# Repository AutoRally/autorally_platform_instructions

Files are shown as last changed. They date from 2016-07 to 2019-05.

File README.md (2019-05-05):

[note]: https://github.com/AutoRally/autorally/wiki/note_icon.png "note"

# AutoRally Platform Instructions

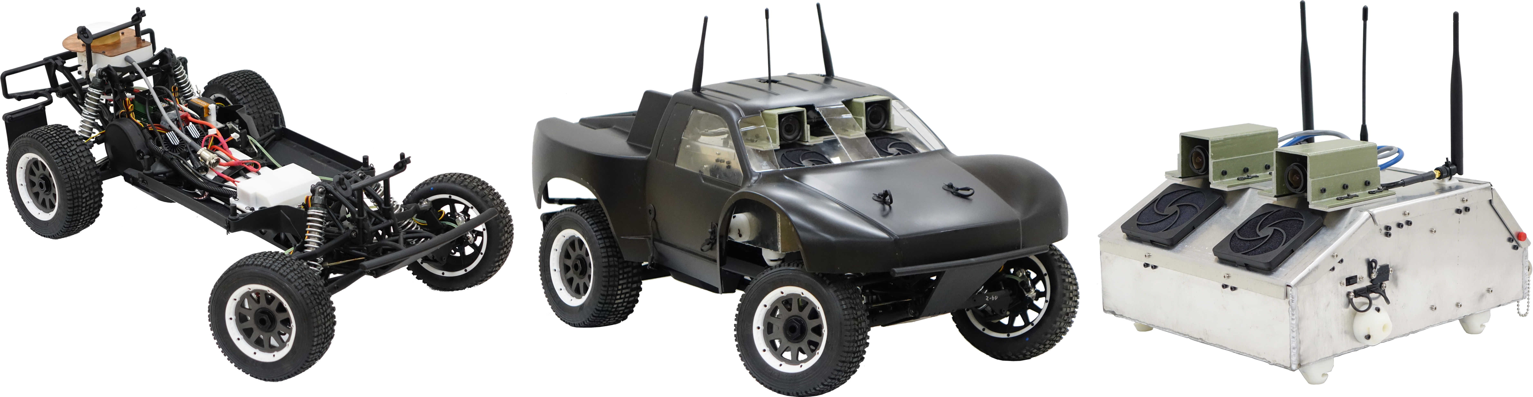
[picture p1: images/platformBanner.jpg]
Platform image


The documents contained in this repository provide all of the information required to construct and operate a complete AutoRally platform. The platform has two primary parts, the chassis and compute box.

A paper detailing the platform and design decisions can be found [here](https://ieeexplore.ieee.org/abstract/document/8616931).

BibTex:
```
@article{goldfain2019autorally,
  title={AutoRally: An Open Platform for Aggressive Autonomous Driving},
  author={Goldfain, Brian and Drews, Paul and You, Changxi and Barulic, Matthew and Velev, Orlin and Tsiotras, Panagiotis and Rehg, James M},
  journal={IEEE Control Systems Magazine},
  volume={39},
  number={1},
  pages={26--55},
  year={2019},
  publisher={IEEE}
}
```

 Please contact us by opening an issue or emailing if you have any questions about the instructions, parts, or any part of the build process.

## Getting Started

Look though the documentation and [Download](https://github.com/AutoRally/autorally_platform_instructions/releases) our latest release. Look over the Getting Started section in the chassis and compute box instruction documents, followed by the parts list and the operating procedures to get a sense of the build process, skill requirements, fabrication methods, and testing procedures. The AutoRally platform can be fabricated by a small team (2-3 students) of non-professionals. The build will go most smoothly if there is at least one person on the team familiar with basic soldering, 3D printing, Ubuntu and ROS configuration. We also link to tutorials for all of the skills required, so any interested party can easily acquire them.

  The most difficult component to fabricate is the compute box enclosure, which may require sending away to a local sheet metal fabrication shop if sheet metal fabrication experience and tools are not available.

Before testing a platform you build, make sure to complete the [Setup Instructions](https://github.com/AutoRally/autorally) and the [Platform Configuration Instructions](https://github.com/AutoRally/autorally/wiki/Platform%20Configuration%20Instructions).

## Included Files:

### autoRally_chassis_instructions

Complete instructions to build an AutoRally chassis.

### autoRally_compute_box_instructions

Complete instructions to build a Mini-ITX AutoRally compute box.

### autoRally_operating_procedures

Document outlining pre-run preparations, starting up and operating the platform, and post-run procedures.

### autoRally_platform_parts_list

Spreadsheet of all parts required to build an AutoRally Platform. The document includes the estimated price, quantities, and link to purchase each component. Parts are organized by vendor, and color coded by where on the platform they are used. The list includes the required parts, parts that help with usability (spare set of batteries), and some common maintenance items.

  The platform uses parts from about 25 suppliers.

  Review the entire list before making any purchases as you may already have some of the parts around such as computer monitors, spare laptops for use as ground station, assorted cables, keyboard and mouse, tools, and supplies. 

### diagrams/

Wiring diagrams for the custom AutoRally chassis and compute box assemblies.

### manuals/

Product manuals for individual parts involved in the build.

### models/

CAD models for components to be fabricated (most will be 3D printed).

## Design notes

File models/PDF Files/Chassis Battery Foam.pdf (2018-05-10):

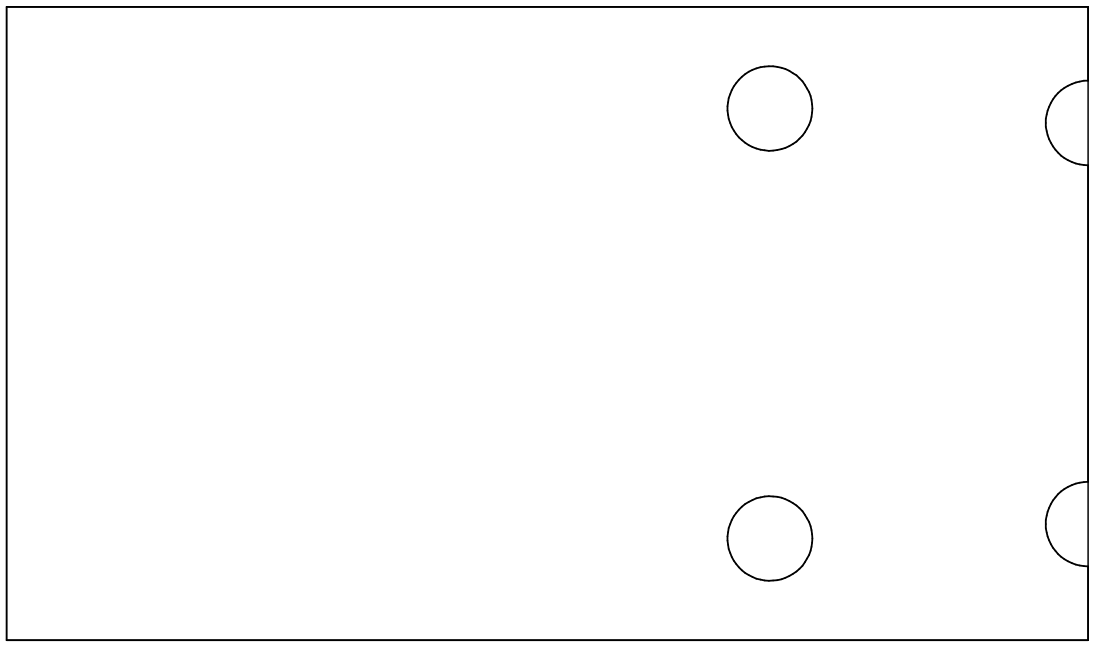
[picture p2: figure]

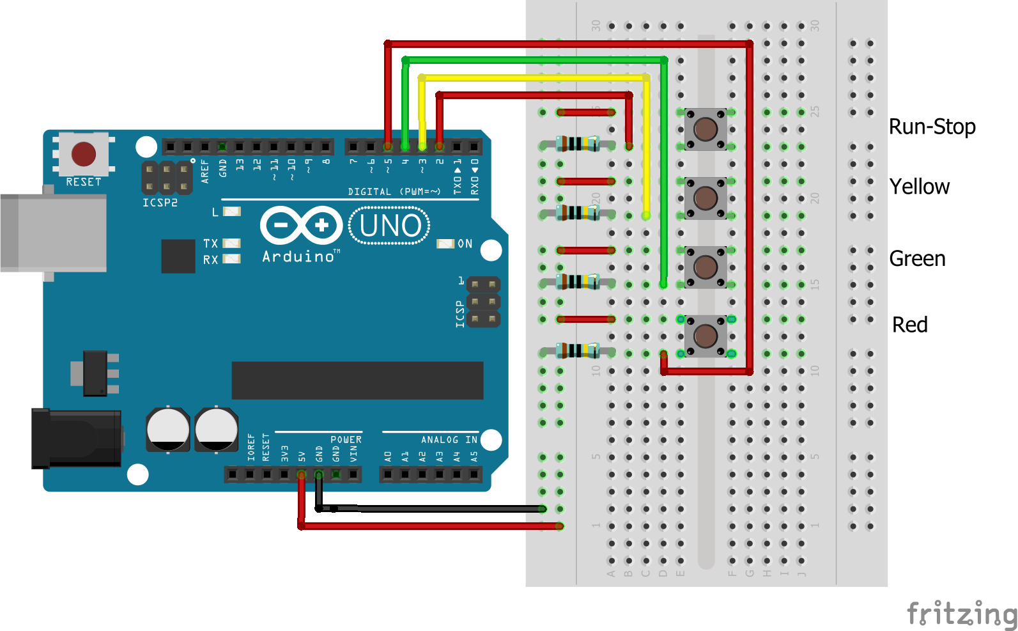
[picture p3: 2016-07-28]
diagrams/AutoRally_RunStop_Schematic_Uno.png

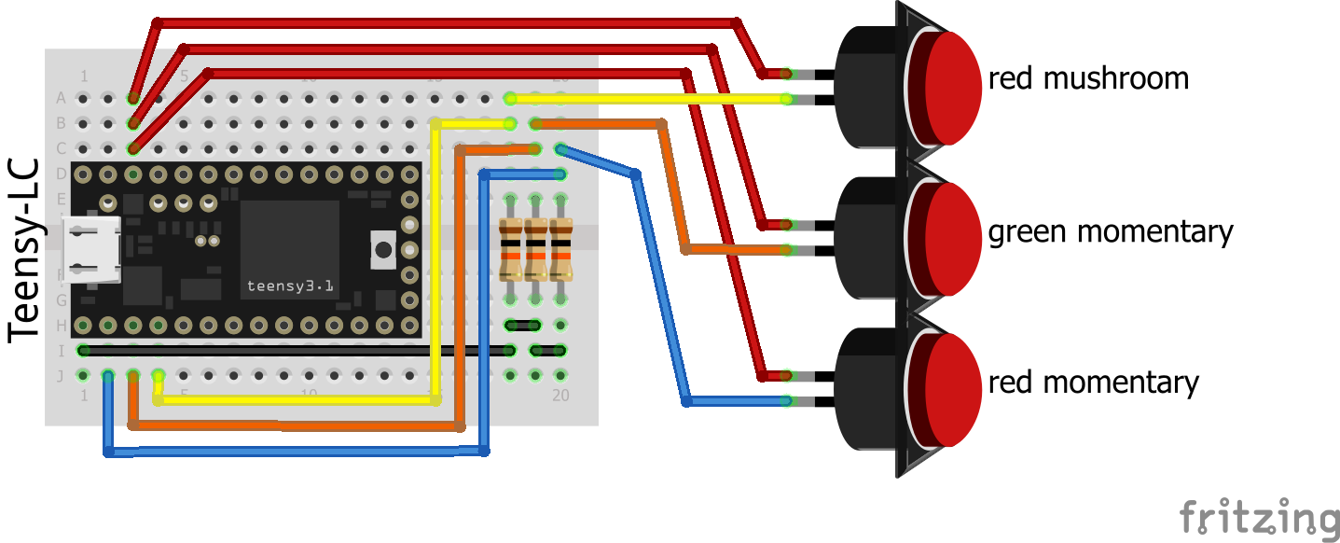
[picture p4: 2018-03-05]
diagrams/AutoRally_RunStop_Schematic_Teensy.png

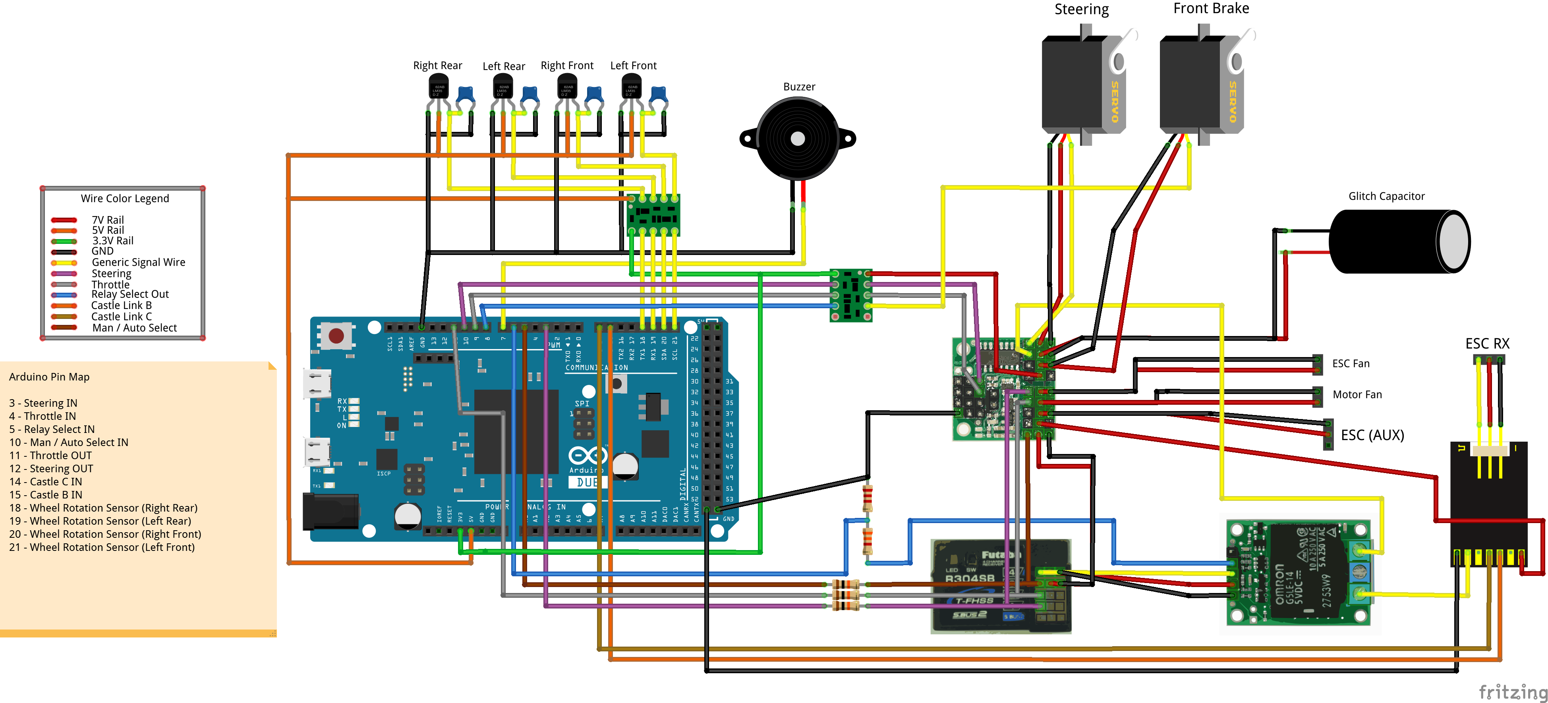
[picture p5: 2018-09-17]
diagrams/AutoRally_Electronics_Box.png

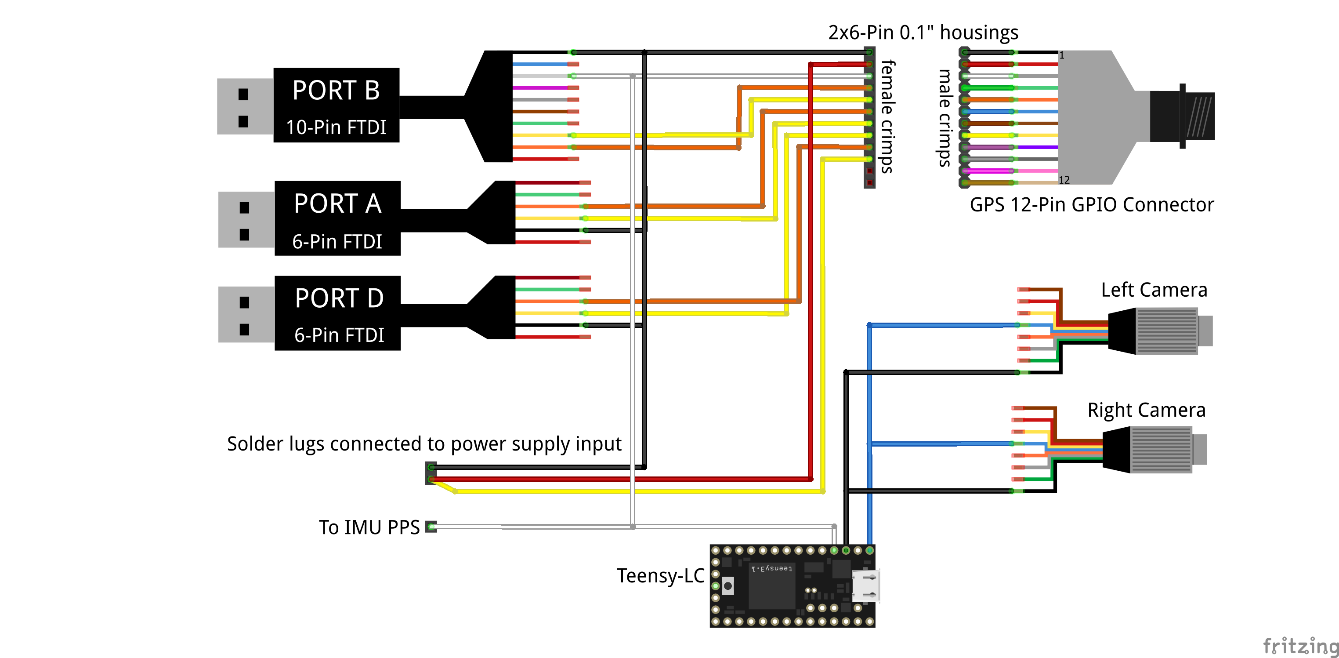
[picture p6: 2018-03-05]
diagrams/AutoRally_ComputeBox_Teensy.png

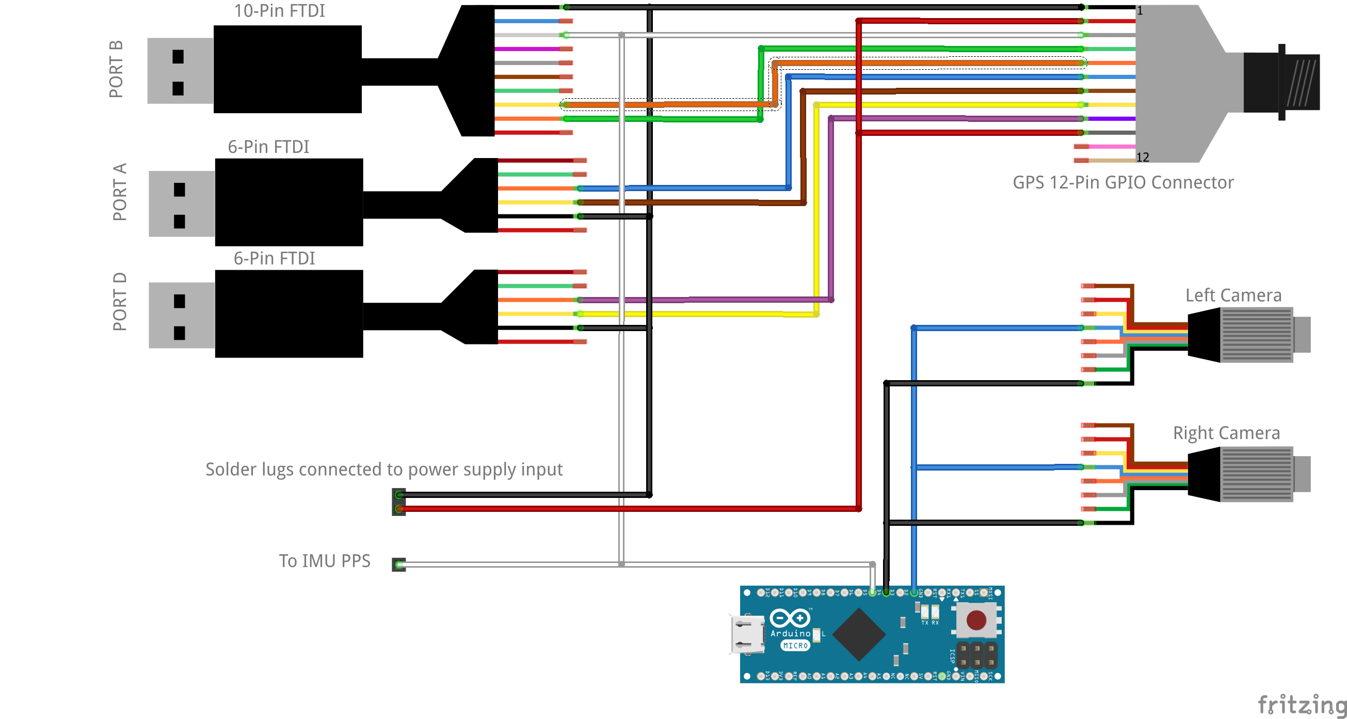
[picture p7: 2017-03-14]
diagrams/AutoRally_ComputeBox_Micro.png

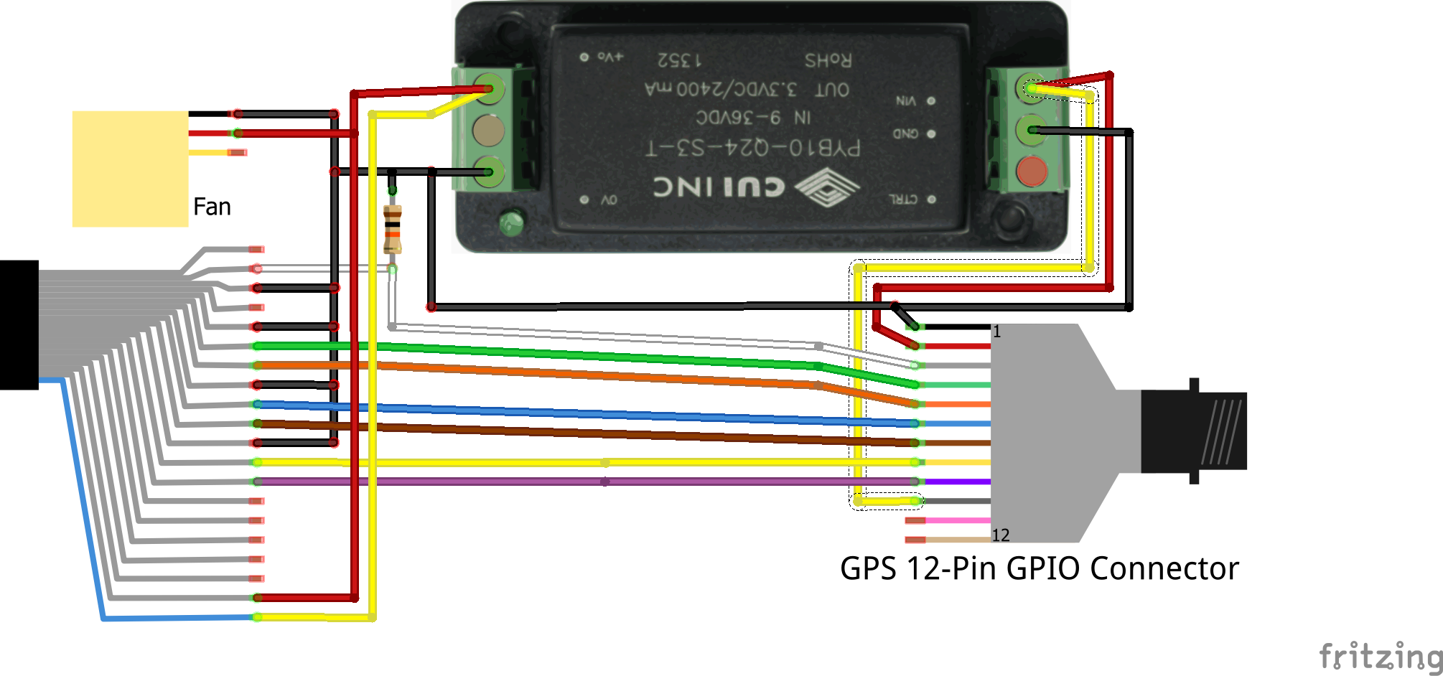
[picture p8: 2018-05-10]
diagrams/AutoRally_GPS_Box.png

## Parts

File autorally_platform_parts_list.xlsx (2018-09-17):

AutoRally Platform Parts List |  |  | Version 1.4 |  | 2018-03-01 |  | Brian Goldfain
This parts list includes all required parts to construct a complete AutoRally chassis and Mini-ITX AutoRally compute box.
Required parts like a monitor, keyboard, and mouse for the compute box, laptop to run operator control station that you likely already have are included in the list, but don't need to be purchased if you already have them.
Tools needed in addition to those included with the chassis are listed at the bottom. There is no need to purchase the tools if you already have access to similar ones.
If your budget allows, the most useful upgrade is a second set of chassis and compute box batteries from MaxAmps.
If you are sending out for the compute box fabrication, you do not need to purchase the raw compute box materials from McMaster
Parts are mostly grouped by seller and each seller is put in a loose category for the platform
 | Color Guide:
 | Compute box raw materials
 | Suggested Maintenance Parts
 | Part Configuration Required Upon Purchase
 | Suggested RTK GPS Base Station Equipment
 | Item | Description | Price | Quantity | Item Totals | Section Totals | Link | Alternate Part
Chassis | RC car chassis | HPI Baja 5SC RTR | $1280.00 | 1 | $1280.00 |  | http://www.davesmotors.com/hpi-109964b-hpi-baja-5sc-1_5-gas-rc-short-course-truck-w_2_4-ghz-radio-black.html
 | Transmitter/Receiver | Futaba 4PV | $279.99 | 1 | $279.99 |  | http://www.davesmotors.com/Futaba-FUTK4700-4PV-4-Channel-T-FHSS-Computer-Radio-System.html
 | Transmitter Battery | LiFe 6.6V 1900mAh 2 Cell Battery | $34.99 | 1 | $34.99 |  | http://www.davesmotors.com/LiFe-6-6V-1900mAh-2-Cell-Battery-Pack.html
 | Battery box eliminator | Team FastEddy Battery Box Eliminator for HPI Baja 5B/5T/5SC | $49.99 | 1 | $49.99 |  | http://www.davesmotors.com/tr800
 | Steering Linkage | Turtle Racing Billet Servo Saver for HPI Baja 5b/5T/5SC | $89.99 | 1 | $89.99 |  | http://www.davesmotors.com/Turtle-Racing-Billet-Servo-Saver-for-HPI-Baja-5b-5T-5SC-TR1481.html
 | Axle extender set | Darksoul V2 Axle Extender Set for HPI Baja 5B/5T/5SC | $59.99 | 1 | $59.99 |  | http://www.davesmotors.com/s.nl/it.A/id.3515/.f
 | Front brakes | Mecatech Front Hydraulic Brake System for HPI Baja 5B/5T/5SC | $329.00 | 1 | $329.00 |  | http://www.davesmotors.com/Mecatech-Front-Hydraulic-Brake-System-for-HPI-Baja-5B-5T-RCTB01013.html
 | Front Tire Foams | Hostile "Zero Growth" Foam Inserts for HPI Baja 5T/5SC Front, and Losi 5ive/DBXL/VEKTA.5 Front/Rear | $44.99 | 1 | $44.99 |  | http://www.davesmotors.com/hostile-zero-growth-foams-hpi-baja-5t-5sc-losi-5ive-desert-buggy-xl-dbxl-HPI4817-LOSB7241-LOS45006.html
 | Rear Tire Foams | Hostile "Zero Growth" Foam Inserts for HPI Baja 5T/5SC Rear | $44.99 | 1 | $44.99 |  | http://www.davesmotors.com/hostile-zero-growth-foams-hpi-baja-5t-5sc-rear-HPI4818-4818.html
 | Alloy Servo Horn 15T | Alloy Horn for Hitec D845/5765/Savox 15T-Spline Servos | $9.99 | 1 | $9.99 |  | http://www.davesmotors.com/alloy-horn-for-multiplex-rhino-digi-4-hitec-5755mg-servo-new-style.html
 | Shock Piston Set | HPI 85413 | $19.99 | 1 | $19.99 |  | http://www.davesmotors.com/hpi-85413-shock-piston-set-for-vvc_hd-shocks.html
 | M4x20mm cap head screws | 10-pack | $1.95 | 1 | $1.95 |  | http://www.davesmotors.com/fg-06725-20-socket-head-cap-screw-set-m4x20mm.html
 | M4x6mm cap head screws | 10-pack | $1.95 | 1 | $1.95 |  | http://www.davesmotors.com/hpi-94502-cap-head-screw-set-m4x6mm.html
 | Body clips 8mm | DDM steel body clips | $3.99 | 1 | $3.99 |  | http://www.davesmotors.com/ddm-steel-body-clips-8mm-for-15-and-18-scale-set-of-50.html
 | Body clips 6mm | HPI 75106 | $5.99 | 1 | $5.99 |  | http://www.davesmotors.com/hpi-75106-body-clip-set-6mm.html
 | Driveshaft | HPI 104966 | $49.49 | 1 | $49.49 |  | http://www.davesmotors.com/hpi-104966-super-heavy-duty-drive-shaft-18x116mm-2pcs.html
 | Front Shock Mounting Set | HPI 85469 | $7.50 | 1 | $7.50 |  | http://www.davesmotors.com/hpi-85469-front-shock-mounting-set.html
 | Axle boots 5SC | HPI 104968, 25x47mm | $11.99 | 2 | $23.98 |  | http://www.davesmotors.com/hpi-104968-axle-boot-25x47mm-4pcs.html
 | Shock Boots Rear | HPI 86443, 20x80mm | $9.99 | 2 | $19.98 |  | http://www.davesmotors.com/hpi-86443-rear-shock-boot-set-20x80mm.html
 | Shock Boots Front | HPI 86442, 20x70mm | $6.30 | 2 | $12.60 |  | http://www.davesmotors.com/hpi-86442-front-shock-boot-set-20x70mm.html
 | Differential Case Gaskets | HPI86478 | $16.99 | 1 | $16.99 |  | http://www.davesmotors.com/hpi-86478-differential-case-gasket-set.html
 | Replacement bearing kit | TeamFastEddy Complete Bearing Upgrade Kit for HPI Baja 5B/5T/5SC | $41.00 | 1 | $41.00 |  | http://www.davesmotors.com/s.nl/it.A/id.4336/.f
 | Axle/transmission grease | Team FastEddy Axle/Transmission Grease | $17.00 | 1 | $17.00 |  | http://www.davesmotors.com/Team-FastEddy-Axle-Transmission-Grease-.html
 | Sway Bar Set | HPI 86618 | $62.99 | 1 | $62.99 |  | http://www.davesmotors.com/hpi-86618-sway-bar-set.html
 | Steering Servo | Savox SV-0235MG | $85.99 | 1 | $85.99 |  | http://www.savoxusa.com/Savox_SV0235MG_Digital_Servo_p/savsv0235mg.htm
 | Brake Servo | Savox SV-1271TG | $79.99 | 1 | $79.99 |  | http://www.savoxusa.com/Savox_SV1271TG_Digital_Servo_p/savsv1271sg.htm
 | Glitch Capacitor | Racer's Edge Glitch Buster Power Capacitor | $5.99 | 1 | $5.99 |  | http://www.savoxusa.com/Glitch_Buster_Power_Capacitor_p/rce2474.htm
 | Electric Conversion Hardware | HPI Baja 5SC Gas to Brushless motor conversion mount kit | $99.99 | 1 | $99.99 |  | https://www.aliexpress.com/item/Rovan-HPI-KM-baja-5B-5T-5SC-Gas-to-Brushless-motor-conversion-mount-kit-851925/32797778803.html
 | Battery Strap Velcro | 20mm x 500mm, 5-pack | $7.99 | 1 | $7.99 |  | https://www.amazon.com/500mm-Rubberized-Non-Slip-Battery-Straps/dp/B01DNFIPAK
 | Heavy duty mounting tape | 1"x50" roll | $4.34 | 1 | $4.34 |  | https://www.amazon.com/Scotch-Indoor-Mounting-1-Inch-125-Inches/dp/B00004Z4A8/
 | Transmitter battery charger | Futaba FUTM1725 | $34.99 | 1 | $34.99 |  | https://www.towerhobbies.com/cgi-bin/wti0001p?&I=LXGFTG
 | Silicone shock fluid | Team Associated Silicone Shock Fluid 60wt, 800cSt | $4.49 | 4 | $17.96 |  | https://www.towerhobbies.com/cgi-bin/wti0001p?&I=LXMZ17
 | Brake Linkage Rod | Linkage rod for MecaTech brakes | $5.23 | 1 | $5.23 |  | https://rc-car-online.de/en/products/y0132-y0132-linkage-rod-for-mecatech-brakes-2-pcs-.html
 | Brake Bleed Kit | FG Filling and ventilation set | $4.48 | 1 | $4.48 |  | https://rc-car-online.de/en/products/fg_9452_02-9452-02-fg-filling-and-ventilation-set.html
 | Throttle Pivot Set | FG Throttle pivot post, 6534/02 | $5.87 | 1 | $5.87 |  | https://rc-car-online.de/en/products/fg_6534_02-6534-02-fg-throttle-pivot-post.html
 | Brake Line | Mecatech brake line, 1 m | $5.98 | 1 | $5.98 |  | https://rc-car-online.de/en/products/mec_1000_62-1000-62-mecatech-brake-line-1-m.html
 | Hydraullic Oil for front brakes | Mecatech brake fluid, 50 ml | $10.85 | 1 | $10.85 |  | https://rc-car-online.de/en/products/mec_1000_60-1000-60-mecatech-brake-fluid-50-ml.html
 | Front Spring |  | $5.53 | 2 | $11.06 |  | http://www.centuryspring.com/compression-spring-10974.html
 | Rear Spring Long |  | $7.83 | 2 | $15.66 |  | http://www.centuryspring.com/compression-spring-2768.html
 | Electric Conversion | Castle Creations 2028 motor and XL-X ESC | $403.71 | 1 | $403.71 |  | http://www.castlecreations.com/en/mamba-xl-x-2028-combo-010-0142-00
 | Castle Serial Link |  | $90.00 | 1 | $90.00 |  | http://www.castlecreations.com/en/serial-link-010-0121-00
 | Castle Link Programmer |  | $20.15 | 1 | $20.15 |  | http://www.castlecreations.com/en/pc-software-and-cables-2/castle-link-v3-usb-programming-kit-011-0119-00
 | Pinion Gear | Castle Creations 14-tooth | $12.07 | 2 | $24.14 |  | http://www.castlecreations.com/en/cc-pinion-mod-1-5-14-tooth-010-0065-24
 | ESC | Castle Creations Mamba XL-X | $193.76 | 1 | $193.76 |  | http://www.castlecreations.com/en/mamba-xl-x-esc-010-0140-00
 | M1.4x6mm screws | 10-pack | $7.80 | 1 | $7.80 |  | http://www.mcmaster.com/#92290a474/=120dvtd
 | M1.4 nuts |  | $2.40 | 4 | $9.60 |  | http://www.mcmaster.com/#91828a005/=120dvjk
 | M3 nylon washer | 100-pack | $2.84 | 1 | $2.84 |  | http://www.mcmaster.com/#95610a530/=120dwf7
 | M3 nylon spacer, 18mm long, 4.5mm OD |  | $1.72 | 6 | $10.32 |  | https://www.mcmaster.com/#93657a508/=1bp3ipn
 | M3x4mm aluminum spacer, 4.5mm OD |  | $0.30 | 10 | $3.00 |  | https://www.mcmaster.com/#94669a097/=1bihasc
 | M3x8mm aluminum spacer, 6mm OD |  | $1.33 | 10 | $13.30 |  | https://www.mcmaster.com/#94669a011
 | M3 hex nut | 100-pack | $2.06 | 2 | $4.12 |  | http://www.mcmaster.com/#90591a250/=120dy5e
 | M3 washer | 100-pack | $1.62 | 1 | $1.62 |  | http://www.mcmaster.com/#93475a210/=131co1z
 | Knob with screw head mount, M3, red | 50-pack | $8.48 | 1 | $8.48 |  | https://www.mcmaster.com/#91175a061/=1bmmsv0
 | M3x6mm screw | 100-pack | $8.56 | 1 | $8.56 |  | http://www.mcmaster.com/#91292a111/=12yr76o
 | M3x8mm screw | 100-pack | $6.58 | 1 | $6.58 |  | http://www.mcmaster.com/#91290a113/=120e123
 | M3x10mm screw | 100-pack | $4.40 | 1 | $4.40 |  | http://www.mcmaster.com/#91292a113/=131cnd2
 | M3x12mm screw | 100-pack | $7.75 | 1 | $7.75 |  | http://www.mcmaster.com/#91290a117/=120e45y
 | M3x16mm screw | 100-pack | $8.20 | 1 | $8.20 |  | http://www.mcmaster.com/#91290a120/=120epou
 | M3x20mm screw | 100-pack | $6.18 | 1 | $6.18 |  | https://www.mcmaster.com/#91292a123/=1bjm0lf
 | M3x25mm screw | 25-pack | $4.80 | 1 | $4.80 |  | https://www.mcmaster.com/#91274a111/=1biy8za
 | M3x35mm screw | 25-pack | $3.40 | 1 | $3.40 |  | https://www.mcmaster.com/#91292a033/=1bhdb06
 | M3x40mm screw | 25-pack | $2.39 | 1 | $2.39 |  | https://www.mcmaster.com/#orders/=1biy9ci
 | M3x50mm screw, for front brakes | 25-pack | $3.39 | 1 | $3.39 |  | http://www.mcmaster.com/#91290a137/=120e644
 | 6-32x1/4" screw | 25-pack | $2.67 | 1 | $2.67 |  | http://www.mcmaster.com/#92185a144/=120dvzz
 | Split loom, 1/2" OD, 5ft |  | $2.52 | 1 | $2.52 |  | http://www.mcmaster.com/#7840k72/=120duy7
 | Rear Spring Short | 6-pack | $11.09 | 1 | $11.09 |  | http://www.mcmaster.com/#9657k408/=zybqrr
 | M4 aluminum spacer, 6mm long, 8mm OD |  | $1.38 | 8 | $11.04 |  | http://www.mcmaster.com/#94669a041/=120elfz
 | M4 nuts | 100-pack | $2.28 | 1 | $2.28 |  | http://www.mcmaster.com/#90591a255/=120em4k
 | M4 washer | 100-pack | $1.86 | 1 | $1.86 |  | https://www.mcmaster.com/#93475a230/=16qk6oh
 | M4x14mm screw | 100-pack | $9.55 | 1 | $9.55 |  | http://www.mcmaster.com/#91290a150/=120enm4
 | M5x16mm button head screws | 10-pack | $8.33 | 1 | $8.33 |  | https://www.mcmaster.com/#97763a822/=1bc84k6
 | 4-40x1/2inch screw | 100-pack | $4.05 | 1 | $4.05 |  | http://www.mcmaster.com/#91773a110/=1382r89
 | 16awg power cable, yellow | 10-ft | $11.40 | 1 | $11.40 |  | https://www.mcmaster.com/#8041k52/=16kwi63
 | Spade Terminal | 100-pack | $8.15 | 1 | $8.15 |  | http://www.mcmaster.com/#69145k59/=12uorg8
 | Clevis Pin 3/8" dia, 5/16" usable | 10-pack | $7.52 | 1 | $7.52 |  | http://www.mcmaster.com/#92390a100/=128m34x
 | Stainless Steel Hinge | 1 ft, 1" Width, 0.133" Knuckle Diameter | $3.33 | 1 | $3.33 |  | https://www.mcmaster.com/#1582a457/=14kexr6
 | Structural Fiberglass 2" rect tube | 5 ft | $30.79 | 1 | $30.79 |  | http://www.mcmaster.com/#8548k23/=128m659
 | Structural fiberglass angle 1"x1" | 5 ft | $9.65 | 1 | $9.65 |  | http://www.mcmaster.com/#8542k51/=128m6ms
 | 6"x12" 6061 Aluminum 0.125" thick |  | $6.86 | 1 | $6.86 |  | https://www.mcmaster.com/#8975k921/=163ji4z
 | 6"x12" 6061 aluminum, 0.25" thick |  | $13.37 | 1 | $13.37 |  | http://www.mcmaster.com/#8975k437/=128mro8
 | 24x36" 3003 aluminum sheet, 0.09" thick |  | $45.97 | 1 | $45.97 |  | http://www.mcmaster.com/#8973k68/=128m88a
 | 12"x24" 5/64" thick clear acrylic sheet |  | $8.15 | 1 | $8.15 |  | https://www.mcmaster.com/#8589k22/=1b53vt2
 | Zip ties, 4" | 100-pack | $2.43 | 2 | $4.86 |  | http://www.mcmaster.com/#7130k52/=120erv8
 | Zip ties, 8.5" | 50-pack | $3.50 | 1 | $3.50 |  | http://www.mcmaster.com/#7130k104/=120evi5
 | Zip tie saddle | 25-pack | $3.43 | 2 | $6.86 |  | http://www.mcmaster.com/#7566k73/=120ew2s
 | Liquid electrical tape, 4oz black |  | $7.89 | 1 | $7.89 |  | http://www.mcmaster.com/#76425a51/=120exoz
 | Liquid electrical tape, 4oz red |  | $7.89 | 1 | $7.89 |  | http://www.mcmaster.com/#76425a51/=120eyab
 | Loctite 243 | 0.34 oz | $13.63 | 1 | $13.63 |  | http://www.mcmaster.com/#91458a115/=120e79s
 | Chassis battery pair, matching 4S 9000mah | 6.5 mm gold female | $489.99 | 1 | $489.99 |  | https://www.maxamps.com/maxamps-lipo-9000xl-4s-14-8v-pair-for-8s-x-maxx
 | Compute box battery, 6s 11Ah | 6.5 mm gold female | $399.99 | 1 | $399.99 |  | http://www.maxamps.com/proddetail.php?prod=Lipo-11000-222-Pack
 | Battery Charger and power supply | 6.5mm Gold Male plugs and Dual output 24V power supply | $456.98 | 1 | $456.98 |  | http://www.maxamps.com/EOS0720i-DUO3-6151.htm
 | 6.5mm bullet connectors | Castle Gold connectors | $6.49 | 6 | $38.94 |  | http://www.maxamps.com/Castle-65mm-SET.htm
 | 4mm banana plug |  | $4.00 | 4 | $16.00 |  | http://www.maxamps.com/4mm-SET.htm
 | Noodle Wire 16awg Red | Per foot | $0.99 | 5 | $4.95 |  | http://www.maxamps.com/16AWG-RED.htm
 | Noodle Wire 16awg Black | Per foot | $0.99 | 5 | $4.95 |  | http://www.maxamps.com/16AWG-BLACK.htm
 | Heavy Duty Servo Wire 50' |  | $14.95 | 1 | $14.95 |  | https://www.servocity.com/50-0-heavy-duty-hitec-standard-wire
 |  |  |  |  |  | $5424.14
Sensors and Electronics | Camera | Part FLIR BFS-U3-13Y3C-C , Blackfly S Color 1.3 MP USB3, 1280x1024 | $395.00 | 2 | $790.00 |  | https://www.ptgrey.com/blackfly-s-13-mp-color-usb3-vision-on-semi-python1300
 | Camera GPIO Cable | Part ACC-01-3009, 1m, 6 pins, Hirose HR10 | $25.00 | 2 | $50.00 |  | https://www.ptgrey.com/1-meter-circular-6-pin-pre-wired-gpio-hirose-connector
 | Camera Lens | Part 68-672, c-mount, 3.5mm fixed focal length | $375.00 | 2 | $750.00 |  | https://www.edmundoptics.com/imaging-lenses/fixed-focal-length-lenses/3.5mm-fl-compact-fixed-focal-length-lens/
 | USB A to B, 6 in |  | $2.95 | 1 | $2.95 |  | https://www.adafruit.com/product/900
 | USB A to mini-B, 6in |  | $2.95 | 1 | $2.95 |  | https://www.adafruit.com/product/899
 | HDMI Panel Mount |  | $5.95 | 1 | $5.95 |  | https://www.adafruit.com/products/978
 | Ethernet Panel Mount |  | $4.95 | 1 | $4.95 |  | https://www.adafruit.com/product/909
 | Buzzer, 5V |  | $0.95 | 2 | $1.90 |  | https://www.adafruit.com/product/1536
 | Tiny Breadboard |  | $4.00 | 1 | $4.00 |  | https://www.adafruit.com/product/65
 | IMU, Microstrain 3DM-GX5-25 | 900 deg/s, 20g calibration | $1495.00 | 1 | $1495.00 |  | http://www.microstrain.com/inertial/3dm-gx5-25
 | IMU cable, Mini-DB9 |  | $45.00 | 1 | $45.00 |  | LORD Microstrain part number 6224-0100
 | WiFi Antenna Cable | RP-SMA, 1.75 ft | $17.40 | 2 | $34.80 |  | http://fieldcomponents.com/RPSMAF-LMR240-RPSMAM-Length.html
 | GPS Antenna cable | MCX Male to TNC Male, 0.75 ft | $25.48 | 2 | $50.96 |  | https://fieldcomponents.com/RMCXM-RG316DS-RTNCM-Length.html
 | GPS, Hemisphere Eclipse P307 GPS | 20-pin module with 20Hz, L1/L2, RTK, GLONASS activations included | $270.00 | 1 | $270.00 |  | https://www.subseatechnologies.com/hemisphere-gnss/oem-modules/p306-p307/
 | Hemisphere GNSS OEM Board Universal Development Kit with activations | Must get this UDK to get overall cheaper price for GPS | $1650.00 | 1 | $1650.00 |  | https://www.subseatechnologies.com/hemisphere-gnss/udk/
 | GPS rover antenna, multi-constellation | Antcom 2GNSSA-XT-1 | $578.00 | 1 | $578.00 |  | http://www.navtechgps.com/departments/equipment/antennas/gnss/antcom_active_l1/l2/l5/l_band_gps_and_l1/l2_glonass_in_2_6_diameter_fixed_mount_configuration/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
 | Servo Multiplexor |  | $10.00 | 2 | $20.00 |  | http://www.pololu.com/product/2806
 | RC Switch |  | $10.00 | 2 | $20.00 |  | http://www.pololu.com/product/2804
 | Level Shifter |  | $2.25 | 5 | $11.25 |  | https://www.pololu.com/product/2595
 | 0.1" Straight Male Header |  | $1.00 | 1 | $1.00 |  | http://www.pololu.com/product/965
 | Stranded Wire: Blue, 26 AWG, 70 Feet |  | $4.50 | 1 | $4.50 |  | http://www.pololu.com/product/2626
 | Stranded Wire: Yellow, 26 AWG, 70 Feet |  | $4.50 | 1 | $4.50 |  | http://www.pololu.com/product/2624
 | Stranded Wire: Red, 26 AWG, 70 Feet |  | $4.50 | 1 | $4.50 |  | http://www.pololu.com/product/2622
 | Stranded Wire: Black, 26 AWG, 70 Feet |  | $4.50 | 1 | $4.50 |  | https://www.pololu.com/product/2620
 | 2x5 Pin 0.1" crimp housing | 5-pack | $0.69 | 1 | $0.69 |  | https://www.pololu.com/product/1913
 | 2x6 Pin 0.1" crimp housing | 5-pack | $0.79 | 1 | $0.79 |  | https://www.pololu.com/product/1914
 | 1x1 Pin 0.1" crimp housing | 25-pack | $0.59 | 1 | $0.59 |  | https://www.pololu.com/product/1900
 | 2x1 Pin 0.1" crimp housing | 25-pack | $0.69 | 1 | $0.69 |  | https://www.pololu.com/product/1901
 | 3x1 Pin 0.1" crimp housing | 25-pack | $0.79 | 2 | $1.58 |  | https://www.pololu.com/product/1902
 | 4x1 Pin 0.1" crimp housing | 10-pack | $0.59 | 1 | $0.59 |  | https://www.pololu.com/product/1903
 | 5x1 Pin 0.1" crimp housing | 10-pack | $0.69 | 1 | $0.69 |  | https://www.pololu.com/product/1904
 | 7x1 Pin 0.1" crimp housing | 10-pack | $0.89 | 1 | $0.89 |  | https://www.pololu.com/product/1906
 | Female Crimps |  | $6.00 | 2 | $12.00 |  | http://www.pololu.com/product/1930
 | Male crimps |  | $8.00 | 1 | $8.00 |  | http://www.pololu.com/product/1931
 | Futaba J Connector Female |  | $1.95 | 4 | $7.80 |  | https://www.pololu.com/product/1926
 | Futaba J Connector Male |  | $2.95 | 4 | $11.80 |  | http://www.pololu.com/product/1927
 | Teensey LC |  | $14.65 | 2 | $29.30 |  | https://www.pjrc.com/store/teensylc_pins.html
 | 1/8 inch Magnets | 10-pack | $1.40 | 5 | $7.00 |  | https://www.kjmagnetics.com/proddetail.asp?prod=D21B-N52
 | 2m waterproof usb 2 connector |  | $23.39 | 1 | $23.39 |  | http://www.l-com.com/usb-usb-cable-waterproof-type-a-male-standard-type-b-male-20m
 | 0.5m waterproof panel mount usb 2 |  | $19.53 | 1 | $19.53 |  | http://www.l-com.com/usb-usb-cable-waterproof-panel-mount-type-a-female-standard-type-a-male-05m
 | USB 3.0 A to microB, 0.5m |  | $18.13 | 2 | $36.26 |  | http://www.l-com.com/usb-usb-30-cable-type-micro-b-a-with-thumbscrew-hardware-05m
 | USB Isolator |  | $149.00 | 1 | $149.00 |  | https://www.sealevel.com/product/iso-1-seaiso-single-port-inline-usb-isolator-ul-recognized/
 |  |  |  |  |  | $6117.30
Computing | ASRock Z270M-ITX/ac | LGA 1151 | $108.99 | 1 | $108.99 |  | https://www.newegg.com/Product/Product.aspx?item=N82E16813157742
 | i7 quad 65 W | i7-7700, LGA1151 | $304.99 | 1 | $304.99 |  | https://www.newegg.com/Product/Product.aspx?Item=N82E16819117727
 | GTX 1050Ti SC 4GB |  | $157.99 | 1 | $157.99 |  | https://www.newegg.com/Product/Product.aspx?item=N82E16814487291
 | 32GB DDR4 RAM |  | $309.99 | 1 | $309.99 |  | http://www.newegg.com/Product/Product.aspx?Item=N82E16820231971
 | 1TB M.2 2280 SSD |  | $448.00 | 1 | $448.00 |  | https://www.newegg.com/Product/Product.aspx?Item=N82E16820147595
 | CPU Cooler | Noctua NH-L9i | $39.19 | 1 | $39.19 |  | http://www.newegg.com/Product/Product.aspx?Item=N82E16835608029
 | 4-Pin fan power cable splitter | Noctua NA-SYC1 | $7.95 | 1 | $7.95 |  | https://www.newegg.com/Product/Product.aspx?Item=9SIA9PV3Y61943
 | USB 3.0 19-pin panel mount |  | $14.12 | 1 | $14.12 |  | http://www.newegg.com/Product/Product.aspx?Item=9SIA24G3KG0688
 | USB 3 4-port hub |  | $8.99 | 1 | $8.99 |  | https://www.newegg.com/Product/Product.aspx?item=9SIA6PF5SY4083
 | Gamepad |  | $19.99 | 1 | $19.99 |  | http://www.newegg.com/Product/Product.aspx?Item=N82E16826104402
 | 8 inch P4 extension cable |  | $2.29 | 1 | $2.29 |  | https://www.newegg.com/Product/Product.aspx?Item=9SIA6705VF9079
 | Wifi antenna pair 2.4/5.8 ghz |  | $5.99 | 4 | $23.96 |  | http://www.newegg.com/Product/Product.aspx?Item=9SIA3M31HT9189
 | USB 3.0 hub, 7 port with power supply |  | $24.99 | 1 | $24.99 |  | https://www.newegg.com/Product/Product.aspx?Item=9SIA1DS14S2069
 | Wireless keyboard/mouse |  | $34.19 | 1 | $34.19 |  | https://www.newegg.com/Product/Product.aspx?Item=N82E16823126188
 | Computer Monitor | for compute box, 27 inch QHD w/ HDMI input | $329.00 | 1 | $329.00 |  | https://www.newegg.com/Product/Product.aspx?Item=N82E16824014591&ignorebbr=1
 | Y-PWR Hot Swap |  | $20.00 | 1 | $20.00 |  | http://www.mini-box.com/Y-PWR-Hot-Swap-Load-Sharing-Controller
 | M4-ATX power supply |  | $90.00 | 1 | $90.00 |  | http://www.mini-box.com/M4-ATX
 | GPS box fan |  | $19.93 | 1 | $19.93 |  | http://www.digikey.com/product-detail/en/UF3F3-500/259-1532-ND/1953953
 | 20 pin GPS ribbon Cable |  | $7.48 | 2 | $14.96 |  | http://www.digikey.com/product-detail/en/TCSD-10-S-12.00-01-N/SAM8541-ND/1106679
 | USB micro plug breakout |  | $3.95 | 2 | $7.90 |  | http://www.digikey.com/product-search/en?keywords=1568-1192-ND
 | Capacitors |  | $0.32 | 10 | $3.20 |  | http://www.digikey.com/product-detail/en/SR151A200JAR/478-7724-ND/3661264
 | 820 Ohm Resistor, 1/4W |  | $0.04 | 10 | $0.40 |  | http://www.digikey.com/product-detail/en/CF14JT820R/CF14JT820RCT-ND/1830348
 | 2 Ohm resistor, 3W |  | $0.57 | 10 | $5.70 |  | https://www.digikey.com/product-detail/en/vishay-bc-components/AC03000002008JAC00/PPC3W2.0CT-ND/596625
 | 2.2 kOhm resistor, 1/4W |  | $0.04 | 10 | $0.40 |  | https://www.digikey.com/product-detail/en/stackpole-electronics-inc/CF14JT2K20/CF14JT2K20CT-ND/1830358
 | 3.3 kOhm resistor, 1/4W |  | $0.04 | 10 | $0.40 |  | https://www.digikey.com/product-detail/en/stackpole-electronics-inc/CF14JT3K30/CF14JT3K30CT-ND/1830362
 | 10 kOhm resistor, 1/4W |  | $0.03 | 25 | $0.72 |  | https://www.digikey.com/product-detail/en/stackpole-electronics-inc/CF14JT10K0/CF14JT10K0CT-ND/1830374
 | Hall Effect Sensors |  | $1.67 | 10 | $16.70 |  | http://www.digikey.com/product-search/en?mpart=OH090U&vendor=365
 | Arduino Due |  | $37.40 | 1 | $37.40 |  | http://www.digikey.com/product-search/en?keywords=1050-1049-ND
 | Due protoshield |  | $14.95 | 1 | $14.95 |  | http://www.digikey.com/product-search/en?keywords=1528-1048-ND
 | Copper foil sheet 11.5 inch x 12 inch |  | $16.54 | 2 | $33.08 |  | http://www.digikey.com/product-detail/en/3m-tc/11.5X12-6-1126/3M9885-ND/2649430
 | EMI Sheilding Textile, 1 inch width, 33 m long |  | $73.10 | 1 | $73.10 |  | https://www.digikey.com/products/en?keywords=732-10216-ND
 | CUI 3.3V 2.4A isolated power supply for GPS |  | $33.35 | 1 | $33.35 |  | http://www.digikey.com/products/en?keywords=PYB10-Q24-S3-T
 | 80mm fan cover |  | $1.60 | 2 | $3.19 |  | http://www.digikey.com/product-detail/en/WMG80M/1053-1402-ND/2621308
 | 80mm EMI filter guard |  | $8.31 | 2 | $16.62 |  | http://www.digikey.com/product-search/en?keywords=Q330-ND
 | 80mm fan filter guard assembly |  | $1.76 | 2 | $3.52 |  | http://www.digikey.com/product-search/en?keywords=1053-1394-nd
 | UART-USB 3.3V |  | $26.00 | 1 | $26.00 |  | http://www.digikey.com/product-search/en?mpart=C232HD-DDHSP-0&vendor=768
 | TTL-USB 3.3V |  | $24.64 | 2 | $49.28 |  | http://www.digikey.com/product-search/en?mpart=TTL-232RG-VREG3V3-WE&vendor=768
 | LED IP-67 |  | $12.81 | 1 | $12.81 |  | http://www.digikey.com/product-search/en?keywords=679-2750-ND
 | XBee Pro 900 MHz RPSMA |  | $39.00 | 2 | $78.00 |  | http://www.digikey.com/product-search/en?keywords=602-1299-ND
 | XBee adapter board |  | $24.99 | 2 | $49.98 |  | http://www.digikey.com/product-detail/en/32400/32400-ND/2666947
 | 900 MHz whip antenna |  | $20.00 | 1 | $20.00 |  | http://www.digikey.com/product-search/en?keywords=A09-HSM-7-ND
 | 900 MHz duck antenna |  | $9.00 | 1 | $9.00 |  | http://www.digikey.com/product-detail/en/digi-international/A09-HASM-7/A09-HASM-7-ND/3482047
 | RPSMA cable 12 inch |  | $10.00 | 1 | $10.00 |  | http://www.digikey.com/product-search/en?keywords=602-1066-ND
 | Power button |  | $13.23 | 1 | $13.23 |  | http://www.digikey.com/product-detail/en/ULV4F2BSS544/EG5194-ND/5299304
 | Reset button |  | $11.53 | 1 | $11.53 |  | http://www.digikey.com/product-search/en?keywords=EG5192-ND
 | Rocker Switch |  | $3.26 | 1 | $3.26 |  | https://www.digikey.com/product-detail/en/e-switch/WB242D1121/EG4758-ND/2116237
 | 80 mm x 25 mm fan |  | $16.94 | 2 | $33.88 |  | http://www.digikey.com/product-search/en?keywords=603-1763-ND
 | 4-pin fan connector |  | $0.89 | 5 | $4.45 |  | http://www.digikey.com/product-search/en?keywords=WM3285-ND
 | Fan connector crimps |  | $0.11 | 25 | $2.84 |  | http://www.digikey.com/product-detail/en/0008500114/WM1114-ND/26475
 | USB dust cover |  | $1.58 | 5 | $7.90 |  | http://www.digikey.com/product-search/en?keywords=MUSB-2A111-024BP-ND
 | Ethernet dust cap |  | $0.59 | 5 | $2.95 |  | https://www.digikey.com/product-detail/en/wurth-electronics-inc/726154101/732-3804-ND/3124561
 | 0.1” header keying plug |  | $0.15 | 10 | $1.52 |  | http://www.digikey.com/product-search/en?keywords=askp01-nd
 | 12 position plug | Hirose RM, 15mm | $20.17 | 1 | $20.17 |  | https://www.digikey.com/product-detail/en/hirose-electric-co-ltd/RM15QPS-12PH(71)/H124340-ND/5134352
 | 12 position receptacle | Hirose RM, 15mm | $20.35 | 1 | $20.35 |  | https://www.digikey.com/product-detail/en/hirose-electric-co-ltd/RM15QRD-12S(71)/H124351-ND/5134358
 | 2 pos power plug | Hirose RM, 15mm | $20.18 | 1 | $20.18 |  | https://www.digikey.com/product-detail/en/hirose-electric-co-ltd/RM15QPS-2PA(71)/H124342-ND/3978449
 | 2 pos power receptacle | Hirose RM, 15mm | $12.03 | 1 | $12.03 |  | https://www.digikey.com/product-detail/en/hirose-electric-co-ltd/RM15QRD-2SA-71/H124353-ND/3978442
 | Power receptacle dust cover | Hirose RM, 15mm | $18.75 | 1 | $18.75 |  | https://www.digikey.com/product-detail/en/hirose-electric-co-ltd/RM15QR-C(71)/RM15QR-C(71)-ND/5134356 \
 | Connector plug Bushing | Hirose RM, 15mm | $0.82 | 2 | $1.64 |  | https://www.digikey.com/products/en?keywords=RM12BPG-B(71)
 | USB A female to C male, 50 mm | only need if motherboard has USB C | $13.10 | 1 | $13.10 |  | https://www.digikey.com/product-detail/en/wurth-electronics-inc/632905731122/732-8224-ND/5723516
 | 100' 12-conductor cable, 24 awg stranded wire | only need 2 ft per platform | $276.41 | 1 | $276.41 |  | https://www.digikey.com/product-detail/en/alpha-wire/1219-12C-SL005/A1219-12C-100-ND/3702047
 | Mushroom stop button |  | $18.40 | 1 | $18.40 |  | http://www.amazon.com/Mushroom-Emergency-Latching-Button-Station/dp/B008LT328Y/ref=sr_1_14?
 | HDMI dust cover |  | $5.96 | 1 | $5.96 |  | https://www.amazon.com/uxcell-Silicone-Computer-Protector-Female/dp/B016FBO6CA
 | Craft Foam 6 mm |  | $18.48 | 1 | $18.48 |  | https://www.amazon.com/gp/product/B0033M0IX6
 | Craft Foam 2 mm |  | $5.86 | 1 | $5.86 |  | https://www.amazon.com/Foam-Sheet-X12-2mm-Black-pack/dp/B005M2Q9MO
 | Lipo Voltage Monitor |  | $8.21 | 3 | $24.63 |  | http://www.amazon.com/gp/product/B0064SHG0Y/ref=ox_sc_act_title_1?ie=UTF8&psc=1&smid=ATVPDKIKX0DER
 | Heat shrink tube, assorted sizes and colors |  | $28.26 | 1 | $28.26 |  | http://www.amazon.com/Assorted-Heat-Shrink-KIT-Multicolors/dp/B00PHL48Y6/ref=pd_sbs_328_11?
 | Epoxy, 30 minute |  | $11.69 | 1 | $11.69 |  | https://www.amazon.com/Great-Planes-30-Minute-Formula-GPMR6047/dp/B001BHI4JU/ref=pd_sim_21_6?ie=UTF8
 | Lipo Battery Bag, 9 inch x 12 inch |  | $5.99 | 2 | $11.98 |  | https://www.amazon.com/Generic-CoBean-Silver-Battery-Storage/dp/B005HTH78W
 | USB A to B, 1.5 ft |  | $0.93 | 1 | $0.93 |  | https://www.monoprice.com/product?p_id=5438
 | USB A to mini-B, 1.5 feet |  | $1.08 | 2 | $2.16 |  | http://www.monoprice.com/Product?c_id=103&cp_id=10303&cs_id=1030302&p_id=5446&seq=1&format=2
 | USB A to mini-B, 3 feet |  | $0.74 | 2 | $1.48 |  | http://www.monoprice.com/product?c_id=103&cp_id=10303&cs_id=1030302&p_id=3896&seq=1&format=2
 | USB A to micro-B, 1.5f feet |  | $0.69 | 1 | $0.69 |  | http://www.monoprice.com/product?c_id=103&cp_id=10303&cs_id=1030307&p_id=5137&seq=1&format=2
 | USB A to micro-B, 3 feet |  | $0.79 | 1 | $0.79 |  | https://www.monoprice.com/product?p_id=4867
 | USB 3.0 extension, 15 feet |  | $1.95 | 2 | $3.90 |  | https://www.monoprice.com/product?p_id=5435
 | HDMI cable, 10 feet |  | $5.78 | 1 | $5.78 |  | http://www.monoprice.com/product?c_id=102&cp_id=10240&cs_id=1024008&p_id=3959&seq=1&format=2
 | Ethernet Cable Cat 5e, 10 feet |  | $1.70 | 2 | $3.40 |  | http://www.monoprice.com/product?c_id=102&cp_id=10208&cs_id=1020807&p_id=11239&seq=1&format=2
 |  |  |  |  |  | $3093.81
Platform Total: |  |  |  |  | $14635.25
The base station GPS provides RTK corrections to the robot to greatly increase the position accuracy. One GPS base station can send corrections to multiple robots.
One set of Base station equipment and tools can be used for multiple AutoRally platforms, except for the Operator Control Station laptop. Each platform needs an OCS laptop, but if you already have a spare that can be used.
 |  |  | Price | Quantity | Item Totals | Section Totals | Link
Base Station | Laptop for Operator Control Station (OCS) | HP ProBook 440 G5, 1080 screen, 16Gb RAM, 512 GB M2 SSD | $1068.00 | 1 | $1068.00 |  | http://store.hp.com/us/en/pdp/hp-probook-440-g5-notebook-pc-customizable-1mj74av-mb
 | Outdoor AC WiFi access point |  | $528.99 | 1 | $528.99 |  | http://www.newegg.com/Product/Product.aspx?Item=N82E16833168140&cm_re=engenius-_-33-168-140-_-Product
 | Direct Burial Ethernet, 50 feet |  | $49.99 | 1 | $49.99 |  | http://cables4sure.com/cat6-network-outdoor-cables/cat6-network-gell-type-direct-burial-shielded-cable-black-50ft.html
 | USB A to A, 10 ft |  | $1.59 | 1 | $1.59 |  | https://cables4sure.com/usb-a-a-cables/10ft-a-a-usb-cable-white.html
 | Power strip |  | $32.49 | 1 | $32.49 |  | https://www.amazon.com/Belkin-12-Outlet-Pivot-Plug-Protector-BP112230-08/dp/B000JE9LD4/
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

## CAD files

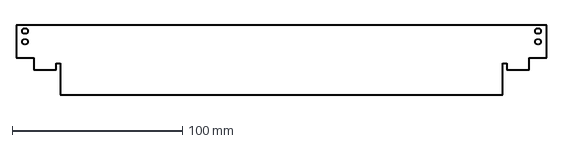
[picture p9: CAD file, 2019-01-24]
models/DXF Files/Compute Box Brace.dxf
312.1 x 40.6 mm

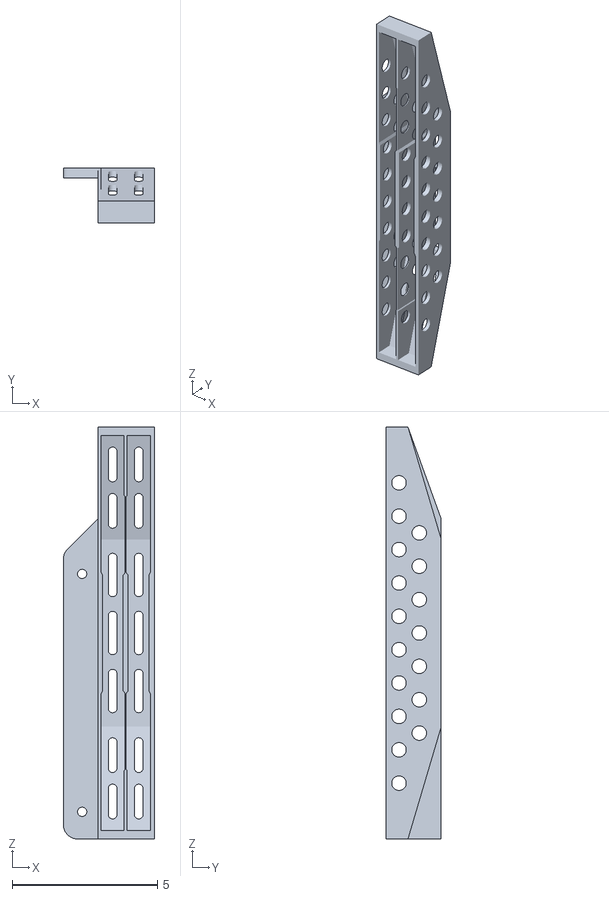
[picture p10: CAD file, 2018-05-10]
models/STL Files/RAM Holder - AsRock.stl
3.15 x 1.90 x 14.2

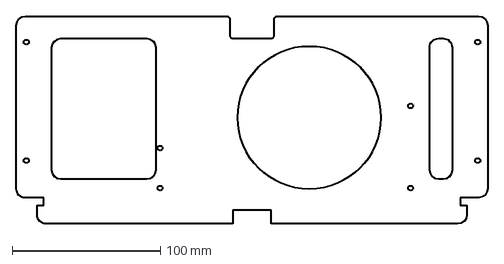
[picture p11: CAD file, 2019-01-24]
models/DXF Files/GPU Strut.dxf
318.1 x 140.0 mm

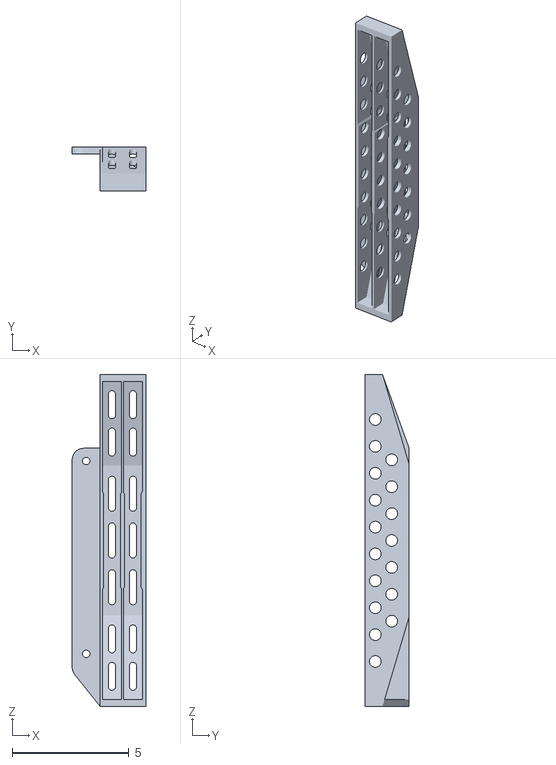
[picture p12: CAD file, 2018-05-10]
models/STL Files/RAM Holder - Asus.stl
3.15 x 1.90 x 14.2

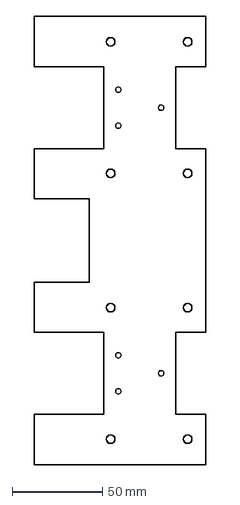
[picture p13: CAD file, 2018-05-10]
models/DXF Files/Camera Mount Bracket.dxf
95.1 x 248.8 mm

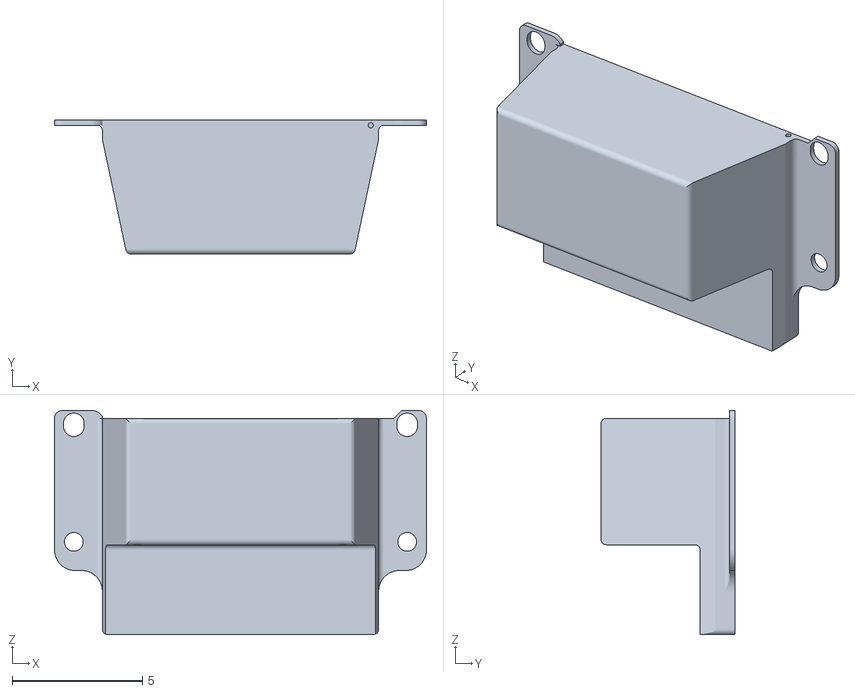
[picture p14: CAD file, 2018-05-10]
models/STL Files/Electronics Box.stl
14.3 x 5.14 x 8.61

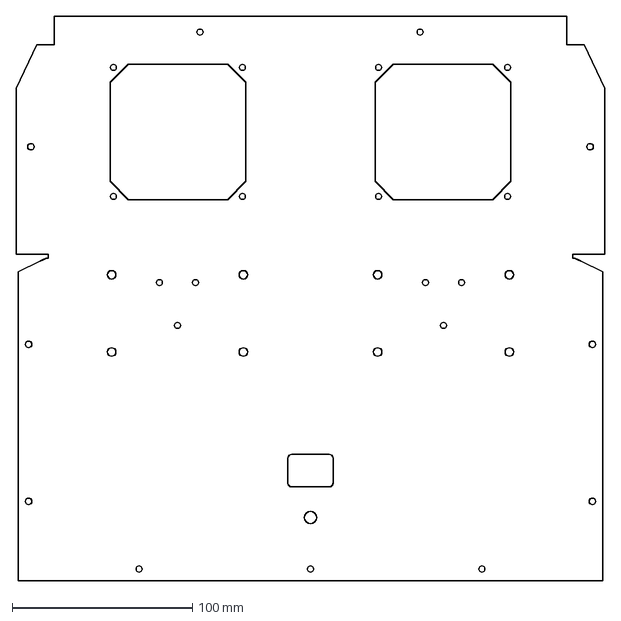
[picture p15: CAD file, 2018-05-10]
models/DXF Files/Compute Box Front Lid.dxf
326.4 x 312.8 mm

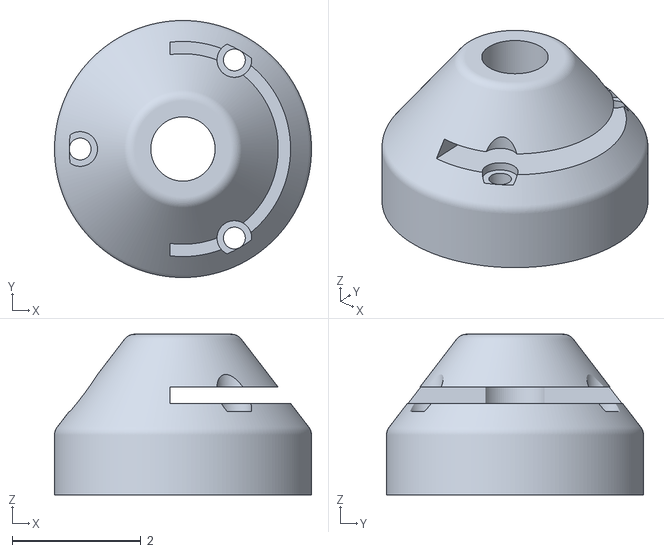
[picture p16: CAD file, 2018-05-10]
models/STL Files/Side Body Mount.stl
4.00 x 4.00 x 2.50

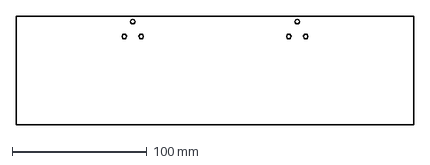
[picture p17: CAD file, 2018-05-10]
models/DXF Files/Compute Box Front Panel.dxf
295.0 x 80.5 mm

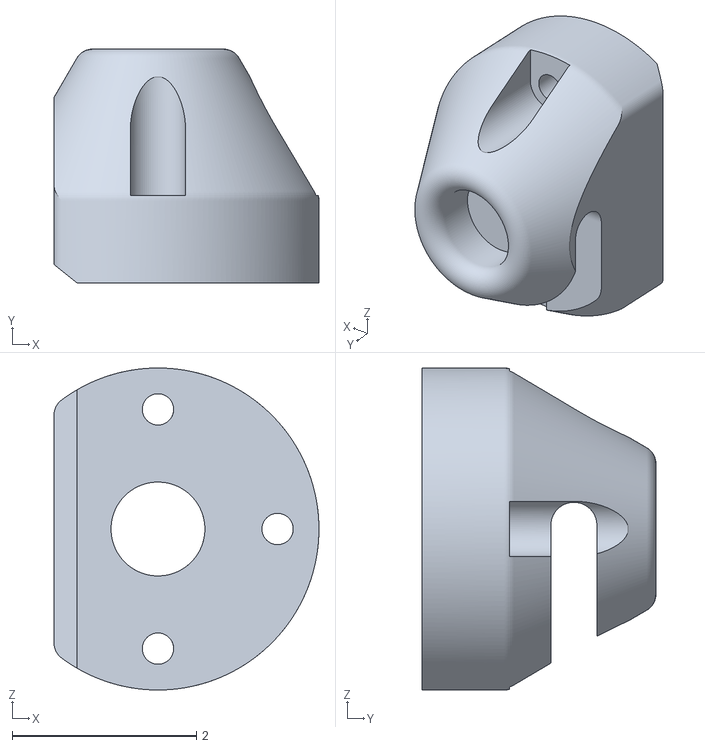
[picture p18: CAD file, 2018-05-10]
models/STL Files/Chassis Mount Rear.stl
2.88 x 2.54 x 3.50

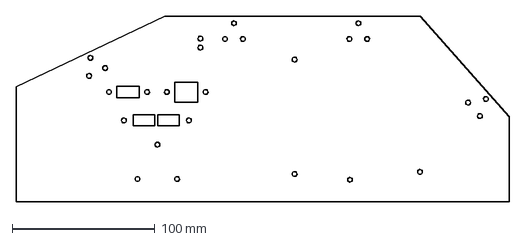
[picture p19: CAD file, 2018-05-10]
models/DXF Files/Compute Box Left Panel.dxf
345.0 x 130.0 mm

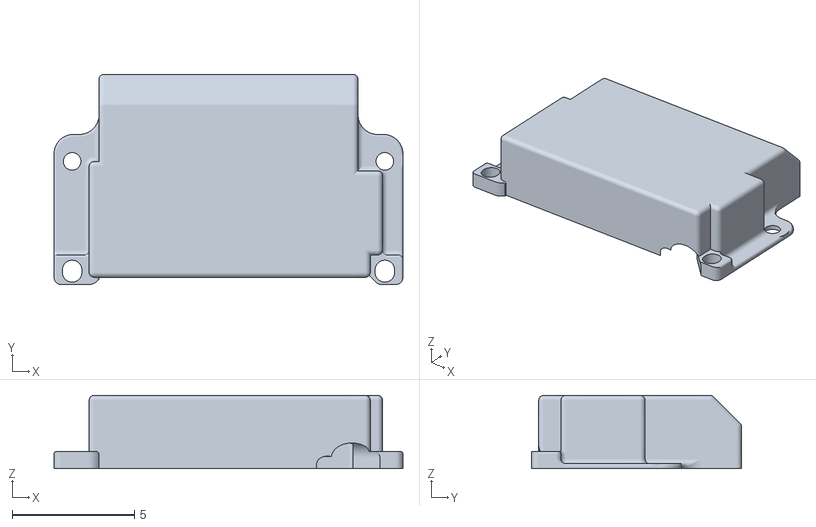
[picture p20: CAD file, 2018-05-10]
models/STL Files/Electronics Box Lid.stl
14.3 x 8.61 x 3.00

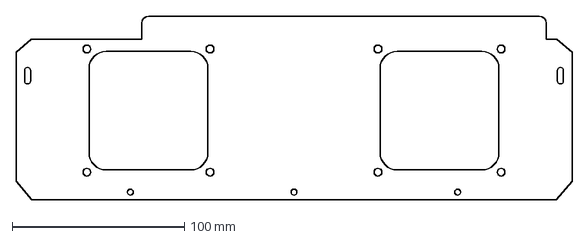
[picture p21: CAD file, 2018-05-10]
models/DXF Files/Compute Box Back Lid.dxf
322.9 x 106.7 mm

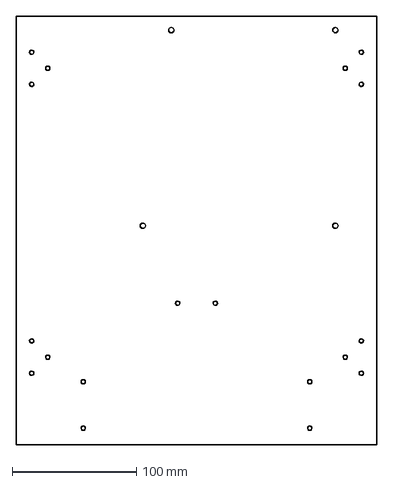
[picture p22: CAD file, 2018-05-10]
models/DXF Files/Compute Box Bottom Panel.dxf
290.0 x 345.0 mm

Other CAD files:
models/STL Files/Chassis Mount Front.stl
models/STL Files/GPU Cover GTX750.stl
models/DXF Files/Compute Box Right Panel.dxf
models/STL Files/GPU Cover GTX1050.stl
models/DXF Files/Compute Box Back Panel.dxf
models/DXF Files/Master Cylinder Plate.dxf
models/STL Files/Arduino Micro Cover Top Plate.stl
models/STL Files/Arduino Micro Cover.stl
models/STL Files/Brake Disk Aligner - Left.stl
models/STL Files/Brake Disk Aligner - Right.stl
models/STL Files/Front Brake Servo Mount.stl
models/STL Files/GPS Box.stl
models/STL Files/Hall Effect Sensor Mount for Rear Hubs.stl
models/STL Files/Wheel Speed Magnet Holder Disk - Front Wheels.stl
models/STL Files/Wheel Speed Magnet Holder Disk - Rear Wheels.stl

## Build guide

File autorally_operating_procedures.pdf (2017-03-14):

# AutoRally Platform Operating Procedures

Version 1.3, February 2017, Georgia Institute of Technology

Contents

## Contents

1 Getting Started | 1
2 Component Operation | 2
3 Pre-run Preparations | 6
4 General Test-Site Setup | 12
5 Operator Control Station (OCS) Hardware Setup | 12
6 Platform Setup | 15
7 Software Configuration | 22
8 Driving Controls | 24
9 What’s Next | 25
10 Platform Shutdown | 25

iii

Contents

11 Test Site Cleanup | 26
12 In Lab Post-Run | 27
13 Appendix A: Test-run Checklist | 30
14 Appendix B: Parts | 31
15 Appendix C: Revision History | 39
16 Appendix D: Contributors | 39

iv

1 GETTING STARTED

## 1 Getting Started

This document describes how to operate an AutoRally platform. Starting from an assembled AutoRally chassis and compute box, you will learn how to operate the platform under autonomous and manual control, perform a pre-run preparations and final configuration at the test site, power on the platform, and run the core AutoRally software. Read through this entire document before operating an AutoRally platform.

The Operating Procedures document assumes that you have constructed and configured an AutoRally chassis and compute box. Complete AutoRally platform build and configuration information can be found at the AutoRally platform instructions (https://github.com/AutoRally/autorally_platform_instructions) and the AutoRally Wiki. (https://github.com/AutoRally/autorally/wiki) In addition to the platform, this document assumes you already have the required Base Station/misc equipment listed in AutoRally Parts List.

The platform is controlled with a standard RC transmitter or by the on-board computer. Seamless remote switching between autonomous and manual control is done with a switch on the transmitter. The last channel on the transmitter, controlled by another button, is a remote run-stop. It controls a live-man relay on the chassis that sits between the throttle signal and electronic speed controller (ESC).

The AutoRally platform is an accessible research testbed, but it can cause serious injury and damage if operated in an unsafe manner. Only operate in an access-controlled space where the operator can maintain line-of-sight visibility to the platform at all times.

This document is best viewed in color.

### 1.1 Battery Safety

Follow all manufacturer provided instructions for safe battery handling.

When connecting batteries always ensure that the ground and positive wires (black and red) of the battery do not touch each other. Physical contact between positive and ground of the battery will cause a power short and permanently damage the batteries and surrounding components.

Avoid all contact between battery wires and the aluminum compute box. The compute box is grounded so any contact with battery leads can short the batteries, potentially through electronics, and will permanently damage the batteries and any components involved in the short. Batteries not in use/connected to anything must have protective battery plugs on wire ends.

When not in use, batteries must be stored inside of LiPo sacks.

### 1.2 Wire Connector Safety

When connecting and disconnecting electrical connections, always apply force to the connectors directly, not to the wires. Pulling and pushing the wires will damage the wires and cause connections to fail prematurely. When disconnecting electrical connections, pull in a straight line, do not twist or apply torque to the connections.

2 COMPONENT OPERATION

### 1.3 Resources and Useful Links

- AutoRally platform instructions (https://github.com/AutoRally/autorally_platform_instructions)
- AutoRally Wiki (https://github.com/AutoRally/autorally/wiki)
- AutoRally Platform Configuration (https://github.com/AutoRally/autorally/wiki/Platform%20Configuration%20Instructions)
- Configuring IP Addresses for the AutoRally Platform (https://github.com/AutoRally/autorally/wiki/Platform%20Configuration%20Instructions)
- Product manuals and datasheets in manuals/

## 2 Component Operation

### 2.1 Transmitter

Parts

- Futaba 4PLS transmitter

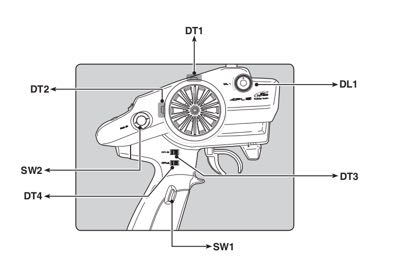
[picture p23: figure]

Figure 1: Transmitter diagram

SW2 is used to switch between manual and autonomous mode. In manual mode only the human operator can control the platform using the transmitter. In autonomous mode the human can still control the platform using the transmitter if no higher priority controllers are running. Refer to the Controlling the AutoRally Platform Wiki Pagefor (https://github.com/AutoRally/autorally/wiki/Controlling%20the%20AutoRally%20Platform) more information on how the servo controller works.

2 COMPONENT OPERATION

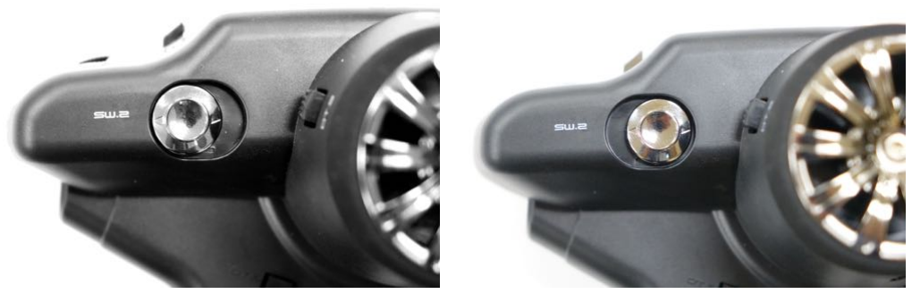
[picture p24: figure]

Figure 2: Left: Autonomous mode. Right: Manual mode

SW1 is used to enable motion. When SW1 is disabled, robot motion is disabled in both autonomous and manual control. You can still control steering when motion is disabled via SW1.

If the platform is moving when motion is disabled, the platform will coast to a stop.

Figure 3: SW1 enables and disables throttle control.

Figure 4: The wheel controls steering.

2 COMPONENT OPERATION

Figure 5: The trigger controls throttle, rear brake, and reverse functionality.

### 2.2 Run-Stop Box

Parts

- Run-stop box

The following is a picture of the run-stop box and operation details:

The red mushroom button and the red momentary switch disables motion through software to stop the platform completely in case of emergencies.To re-enable motion, ensure that the mushroom is released by twisting in the direction indicated on the button and that the green button is pressed.The Run-Stop Box only a↵ects throttle control in autonomous mode.

The green momentary switch of the run-stop box enables motion for the platform.

2 COMPONENT OPERATION

### 2.3 Compute Box

Parts

- Compute box

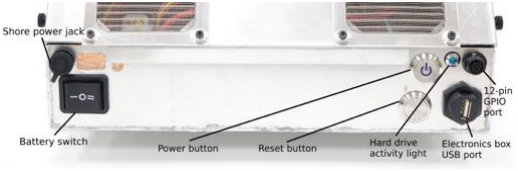
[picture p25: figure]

Figure 6: Labeled diagram of compute box back panel

### 2.4 Shore Power

Parts

- Shore power cable
- 24V MaxAmps power supply

Instructions

a. To use shore power, connect the shore power cable to the shore power connector located on the left side of the compute box, above the battery switch. Do this after it is plugged into a power supply

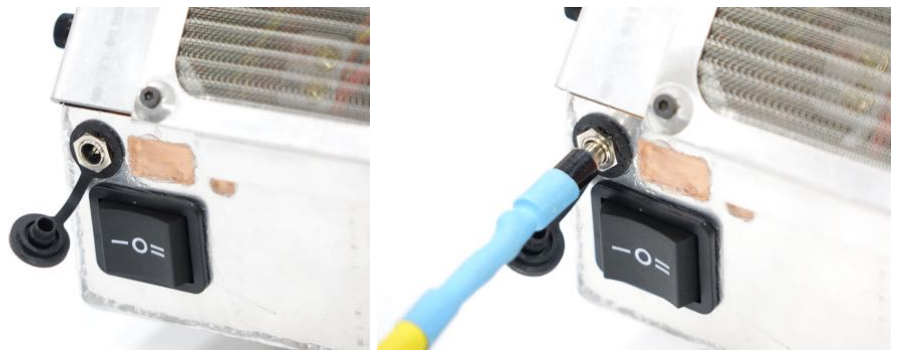
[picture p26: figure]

### 2.5 Compute Box Battery Switch

Parts

- Compute box

3 PRE-RUN PREPARATIONS

The three-way switch on the back of the compute box controls compute box battery operation. The switch position does not a↵ect shore power.

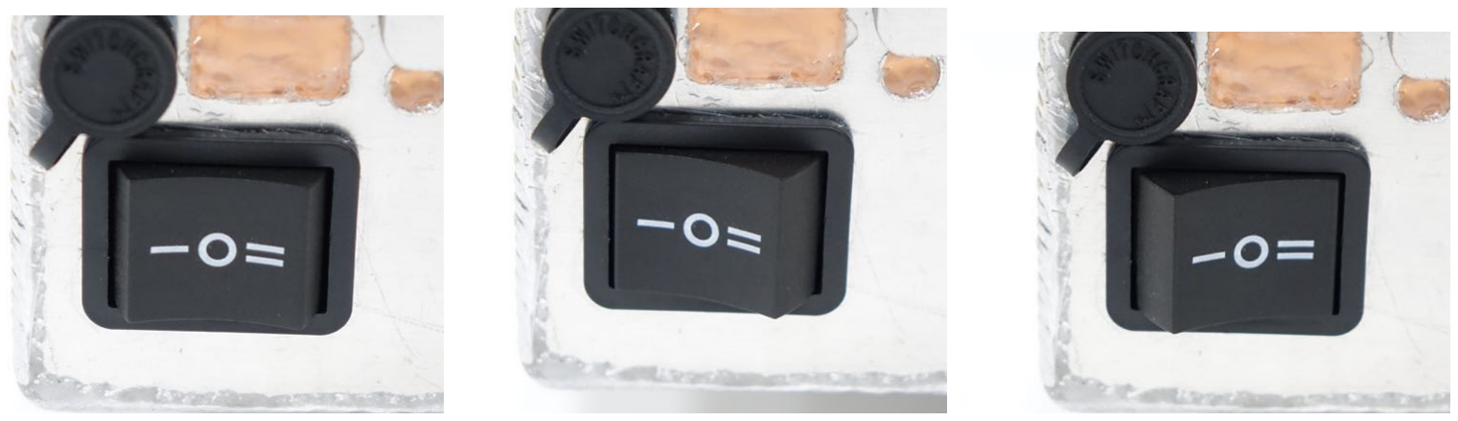
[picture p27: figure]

Figure 7: Left: Position 0- battery power is turned o↵; Center: Position I- compute box runs on battery power; Right: Position II- Charge Mode for compute box battery is enabled.

## 3 Pre-run Preparations

### 3.1 Charge Batteries

Batteries must be supervised and kept in LiPo sack while charging.

Parts

- Hyperion EOS 720i battery charger
- 24V MaxAmps power supply
- Balance charge tab adapters
- 2 6.5mm red charge leads
- 2 6.5mm black charge leads
- Chassis batteries - LiPo 6500mAh 4S 14.8v HPI Baja Pair
- Compute box battery - LiPo 11,000mAh 6S 22.2v battery

Instructions

a. Connect the battery charger to power supply with 4mm banana plugs.

Connect the ground (black) wires first, followed by the positive (red) wires.

b. After charger is connected, connect power supply unit to a power source.

3 PRE-RUN PREPARATIONS

If you connect the charger to the power supply, after connecting power supply to a power source, it will produce a spark.

c. Plug all charge leads into charger according to lead color.

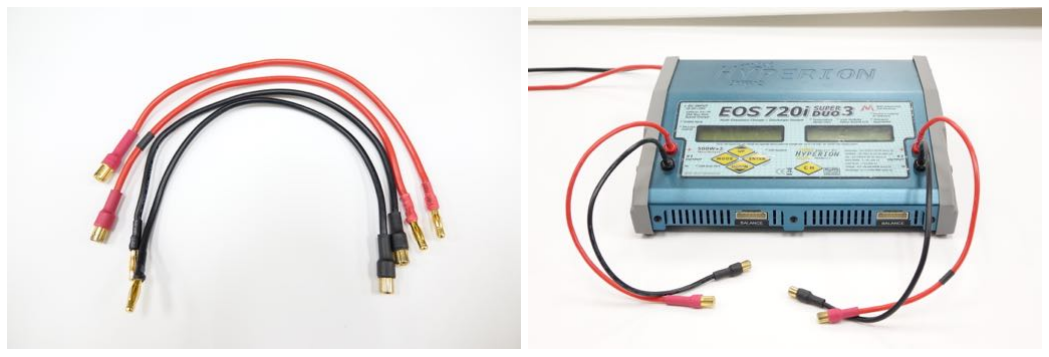
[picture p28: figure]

d. Connect the balance charge adapter to the charger.

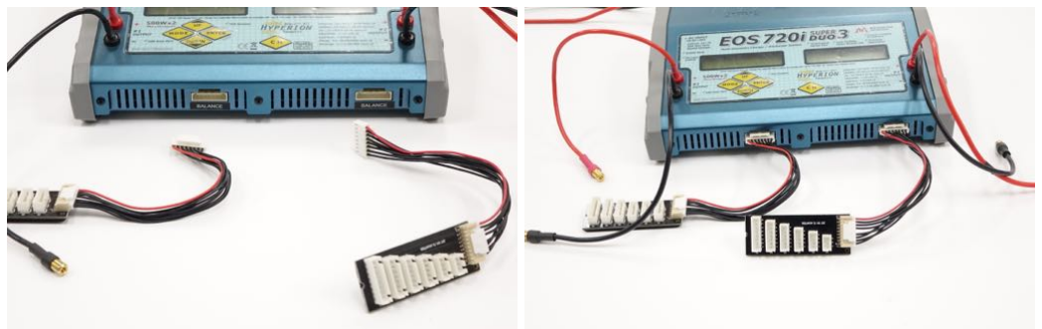
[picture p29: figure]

### 3.1.1 Chassis Batteries

Instructions

a. Connect the 6.5mm charge lead to the chassis battery. Begin with ground (black) and proceed with positive (red). Repeat for the second battery.
b. Connect the battery’s balance tab to the appropriate connector on the balance adapter. Repeat for the second battery.

3 PRE-RUN PREPARATIONS

c. Select charging profile for the chassis batteries. If no profile exists, create one with the following settings.

Use the charger’s manual in the manuals/folder as reference.

LiPo 4 cell, 14.8V battery

1C charge rate at 6.5A

d. Select the Sync charge mode.
e. Charge batteries.

### 3.1.2 Compute Box Battery

Instructions

a. Connect compute box battery to charge leads and balance adpater.

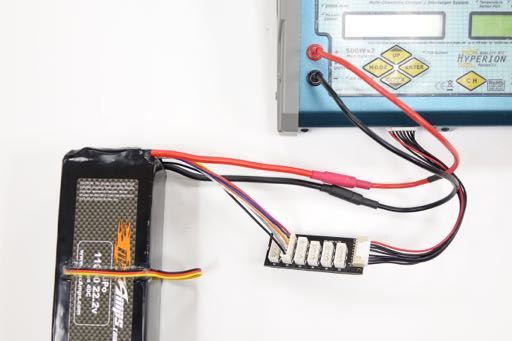
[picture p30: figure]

b. Select charging profile for the compute box battery. If no profile exists, create one with the following settings.

Use the charger’s manual in the manuals/folder as reference.

LiPo 6 cell 22.2V battery

1C charge rate at 11A

c. Select the Solo charge mode.
d. Charge batteries.

3 PRE-RUN PREPARATIONS

### 3.1.3 Compute Box Battery While Installed In Compute Box

Only charge compute box battery with this method when testing outdoors with compute box battery installed in compute box.

Parts

- Compute box w/ compute box battery
- Hyperion EOS 720i battery charger
- Shore power cable
- 24V MaxAmps power supply

Instructions

a. Connect shore power if the compute box will be running while charging the battery.
b. Set the compute box battery switch to position 0.
c. Remove the two thumb screws from the rear hinge panel of the compute box and open rear hinge panel to access compute box battery.
d. If present, disconnect the LiPo monitor from the compute box battery balance tab.
e. Connect the black charger lead to the ground (black) compute box battery charge connector located on the left side of the compute box battery holder. Connect the red charger lead to the positive (red) compute box battery charge connector.

3 PRE-RUN PREPARATIONS

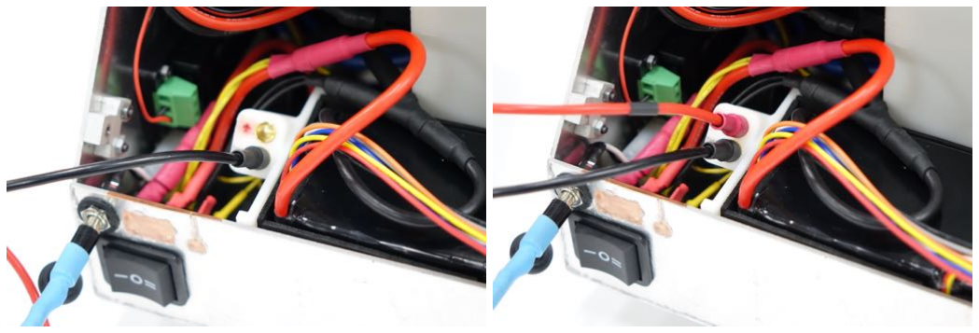
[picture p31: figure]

f. Connect the balance adapter to the balance tab of the compute box battery.
g. Set the battery switch to position II (battery charge mode).
h. Select compute box battery profile on the charger.
i. Charge battery.
j. Set battery switch to position 0, disconnect charging leads and balance adapter, and secure compute box rear panel with two thumb screws.
k. Set battery switch to position I and disconnect shore power to return compute box to battery power.

### 3.2 Update Software

Instructions

3 PRE-RUN PREPARATIONS

a. Update your software and AutoRally software on the compute box and OCS computer.
b. Compile software on compute box and OCS.
c. Test all software launches and ensure they run as expected.

It is recommended to not update Ubuntu software packages unless you are prepared to debug issues that may arise.

### 3.3 Packing List

Make sure to bring the following items with you when you test. Refer to the appendix for pictures of items.

### 3.3.1 Equipment to operate the platform

- AutoRally Chassis
- AutoRally Compute Box
- Platform Body
- Futaba 4PLS Transmitter
- OCS Laptop
- 24V MaxAmps Power Supply
- Chassis Batteries in LiPo sacks
- Compute Box Battery in LiPo sack
- Battery Charger
- Shore Power Cable
- Wireless Access Point with PoE injector and power supply
- Run-Stop Box
- Base station GPS Setup(optional)

### 3.3.2 Equipment to operate the base station

- Monitors with HDMI and power cables
- Keyboards, Mice
- USB Hub
- Extension Cords
- Power Strips
- USB Extension Cables
- Ethernet Cables (minimum of 2)
- Spare screws, nuts, wire plugs, body pins, cotter pins
- Toolbox with all tools

Always pack extra supplies - “When in doubt, bring it out.”

5 OPERATOR CONTROL STATION (OCS) HARDWARE SETUP

## 4 General Test-Site Setup

Parts

- Tables
- Monitors, keyboards and mice
- OCS computer with USB hub
- Shore power cable
- 24V MaxAmps power supply
- Extension power cables and power strips

Instructions

a. Set up the ground station on site (chairs, tables, large tent, etc.). Arrange the ground station in a layout appropriate for your setup.
b. Set up power with extension cords and power strips as necessary.
c. Set up the OCS computer and connect a powered USB hub.
d. Set up monitor, mouse, and keyboard for the compute box.
e. Connect the shore power cable to the 24V MaxAmps power supply. Connect ground (black) wire and positive (red) wire.
f. Connect the power supply to a power source with two power cords.

## 5 Operator Control Station (OCS) Hardware Setup

### 5.1 Wireless Access Point Setup

Parts

- Wireless access point (AP)
- Power over Ethernet (PoE) injector with power supply
- 2 Ethernet cables

Instructions

a. Mount the AP at an elevated position in the middle of your track.
b. Connect one Ethernet cable to the LAN1 (PoE) port on the AP.

5 OPERATOR CONTROL STATION (OCS) HARDWARE SETUP

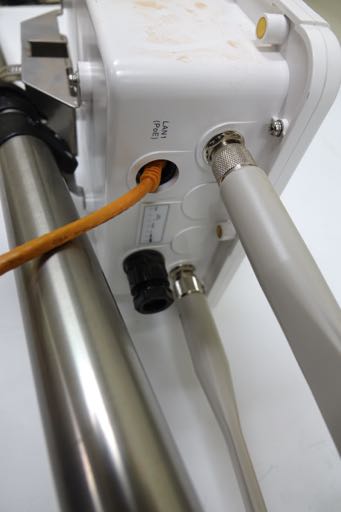
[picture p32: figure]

c. Connect the other end of the same Ethernet cable into the AP/Bridge port of the PoE injector.
d. Connect the second Ethernet cable to the Network Port on the PoE Injector and the OCS computer.

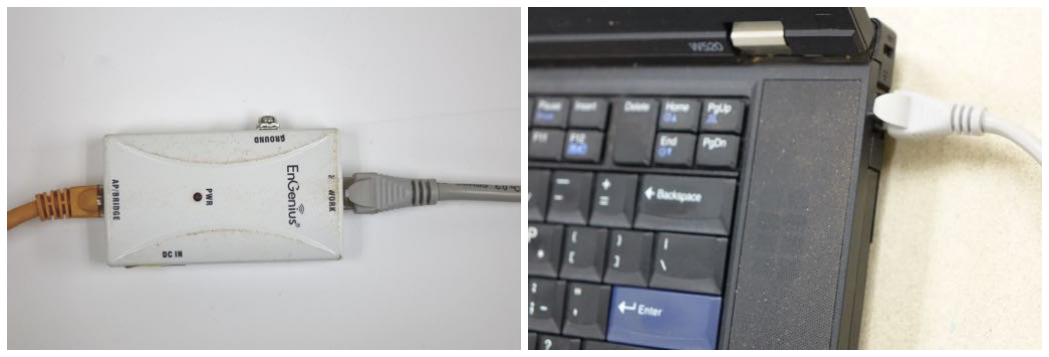
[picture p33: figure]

5 OPERATOR CONTROL STATION (OCS) HARDWARE SETUP

e. Connect the PoE power adpater to the injector and the power source.

### 5.2 Run-Stop Box

Parts

- Run-stop box

Instructions

a. Connect both USB cables from the run-stop box to the OCS USB hub.

### 5.3 Base Station GPS Setup

This section is only necessary if you have a base station GPS.

Parts

- GPS RS320 receiver
- GPS Antenna (L1/L2 GPS, L-Band)
- GPS TNC-TNC antenna cable
- GPS DB-9 data cable
- GPS USB cable
- GPS power adapter
- OCS computer with USB hub

Instructions

a. Set up the antenna stand and mount the antenna.
b. Connect antenna to the RS320 reciever with the TNC-TNC antenna cable.

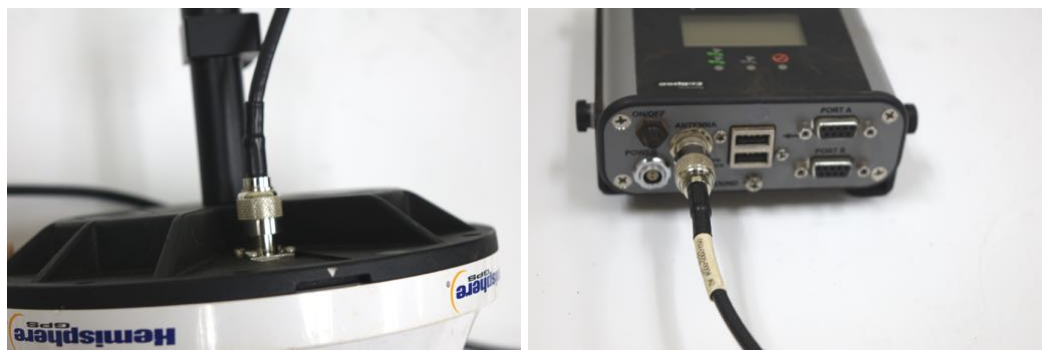
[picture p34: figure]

If your OCS machine does not have a serial port, connect serial to USB adapter to the DB-9 data cable.

c. Connect USB cable to Port A, DB-9 data cable to Port B on the RS320 receiver.
d. Connect the USB ends of these cables from the receiver to the USB hub of the OCS computer.

6 PLATFORM SETUP

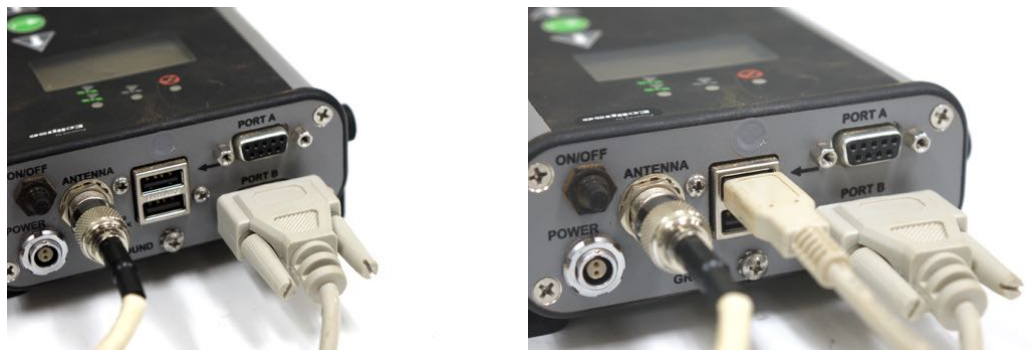
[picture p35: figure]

e. Connect power adapter to the Power port on the receiver. Plug adapter into a power strip.

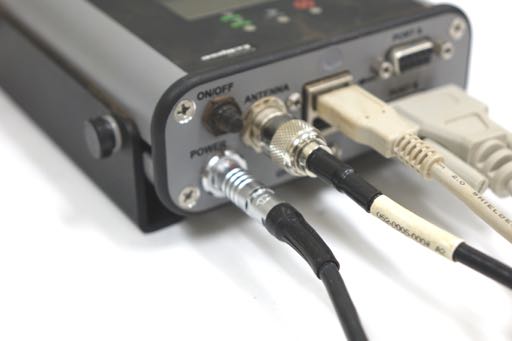
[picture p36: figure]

f. Press the power button on the receiver to turn on the base station GPS.

## 6 Platform Setup

### 6.1 Battery Installation

### 6.1.1 Chassis

Parts

- AutoRally chassis
- Chassis batteries - LiPo 6500mAh 4S 14.8v HPI Baja Pair
- Baja series adapter
- Chassis battery velcro strap

Instructions

a. Use the Baja series adapter to connect the ground lead of the chassis battery with the pre-charge circuit to the positive lead of the other chassis battery with the Baja series adapter.

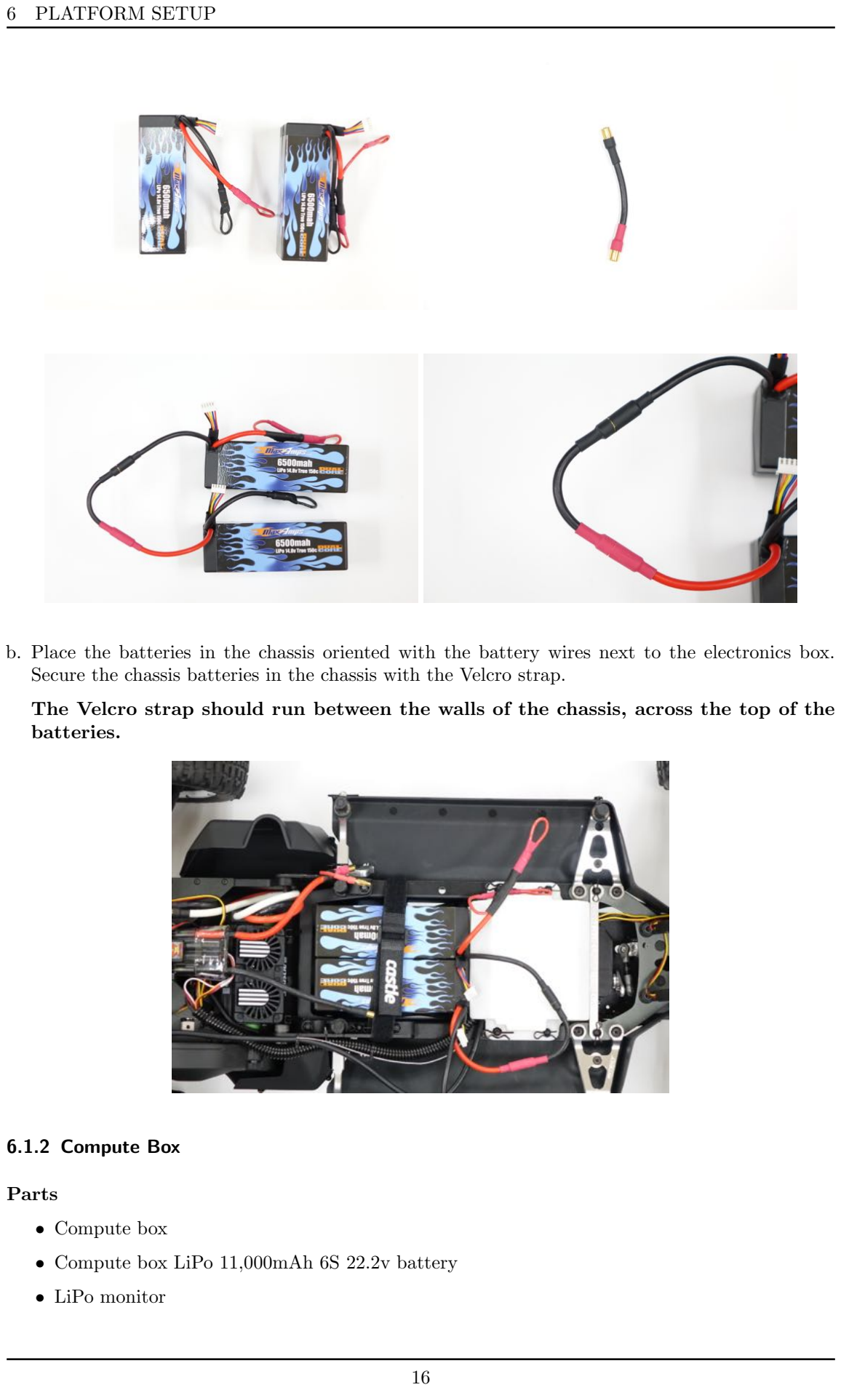
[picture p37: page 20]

6 PLATFORM SETUP

b. Place the batteries in the chassis oriented with the battery wires next to the electronics box. Secure the chassis batteries in the chassis with the Velcro strap.

The Velcro strap should run between the walls of the chassis, across the top of the batteries.

### 6.1.2 Compute Box

Parts

- Compute box
- Compute box LiPo 11,000mAh 6S 22.2v battery
- LiPo monitor

6 PLATFORM SETUP

Instructions

a. If compute box is mounted on the chassis, remove it from the chassis.
b. Remove the two thumb screws that secure the back panel and open the rear hinge panel to expose the compute box battery slot.

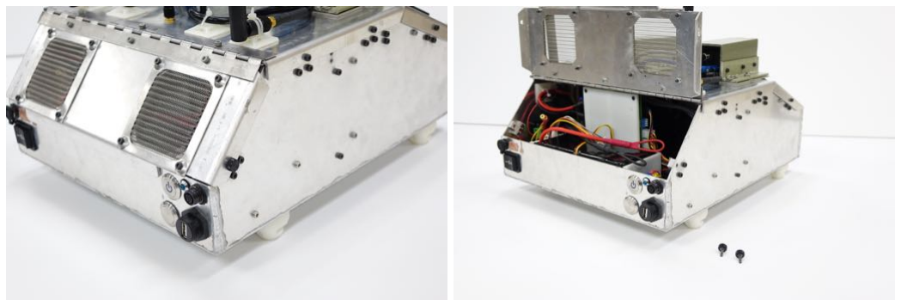
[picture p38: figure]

c. Install the compute box battery in the compute box battery slot with the leads oriented to the left.

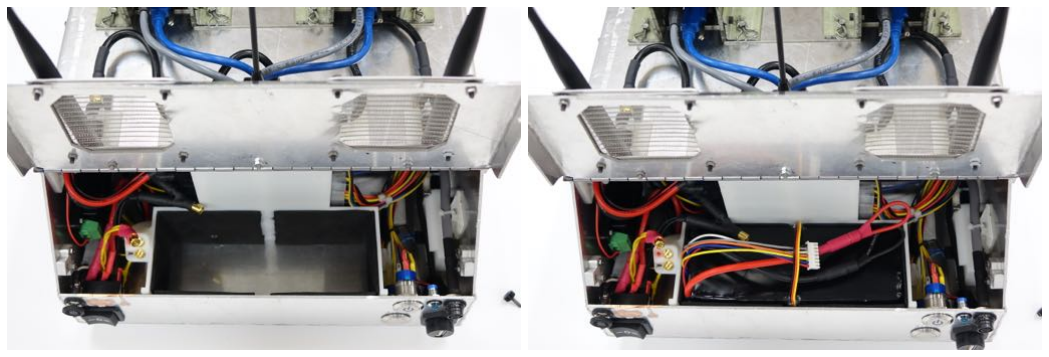
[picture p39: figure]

d. Verify that the compute box battery switch is set to position 0.
e. Connect the 6.5mm ground (black) wire of the battery to the 6.5mm ground connection of the compute box. Connect the 6.5mm positive (red) wire of the battery to the 6.5mm positive connection of the compute box.

6 PLATFORM SETUP

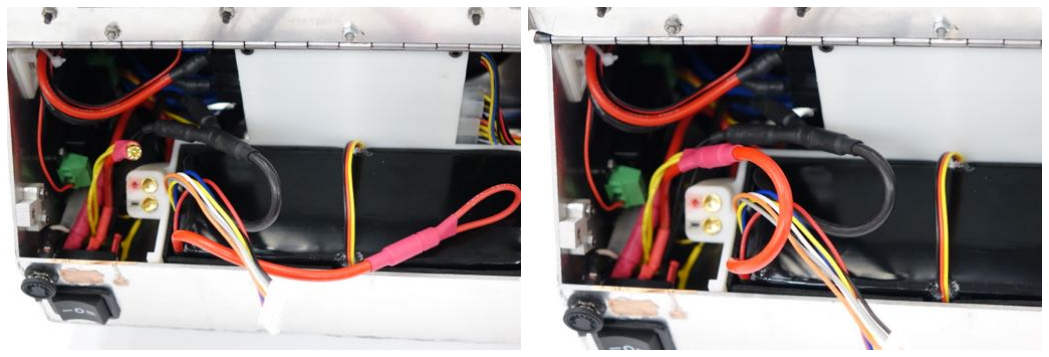
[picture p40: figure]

f. Install a LiPo monitor on the balance tab of the compute box battery.
g. Close rear hinge panel and re-install thumb screws on rear side of compute box.

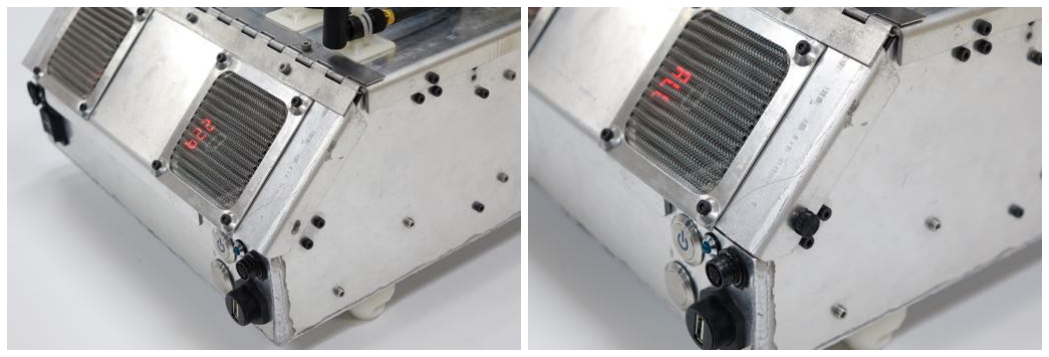
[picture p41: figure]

### 6.2 Powering the Chassis

Parts

- Futaba 4PLS transmitter
- AutoRally chassis with batteries installed
- 2 LiPo monitors

Instructions

a. It may be beneficial to confirm the software is operating correctly before continuing with powering the chassis to prevent draining the batteries unnecessarily.

6 PLATFORM SETUP

b. Turn the transmitter on. Reference the Transmitter Operation diagram in the Getting Started section or the transmitter manual for transmitter functionality.
c. Connect the 6.5mm ground (black) wire of the battery to the ground wire of the ESC.

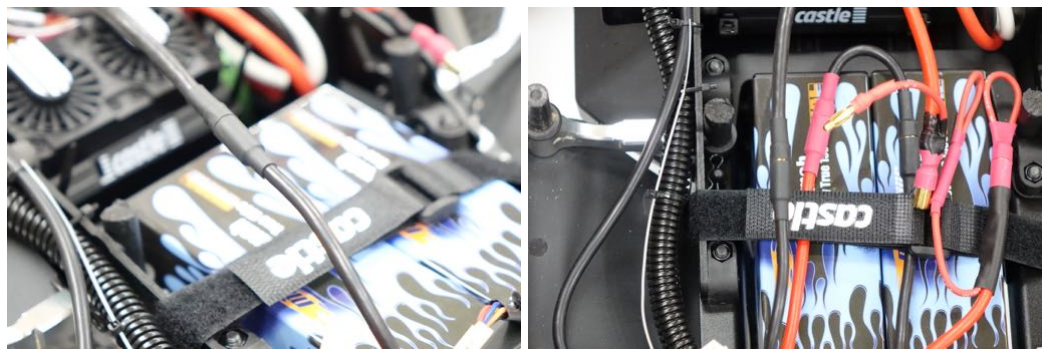
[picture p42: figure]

d. Complete the next two steps quickly so that the pre-charge circuit does not overheat. Connect the 4mm positive (red) pre-charging wire from the battery to the corresponding 4mm positive wire on the ESC.
e. Connect the larger 6.5mm positive (red) wire from the battery into the corresponding 6.5mm positive wire on the ESC.
f. Install a LiPo monitor onto the balance tab of each chassis battery.

6 PLATFORM SETUP

### 6.3 Mounting the Compute Box

Parts

- Compute box with battery installed
- Chassis with battery installed
- Large body clips

Instructions

a. Mount compute box to chassis by lining up the four chassis mounts on the compute box with the chassis body mounts. Push the compute box down so that the compute box chassis mounts fully cover the body mounts.

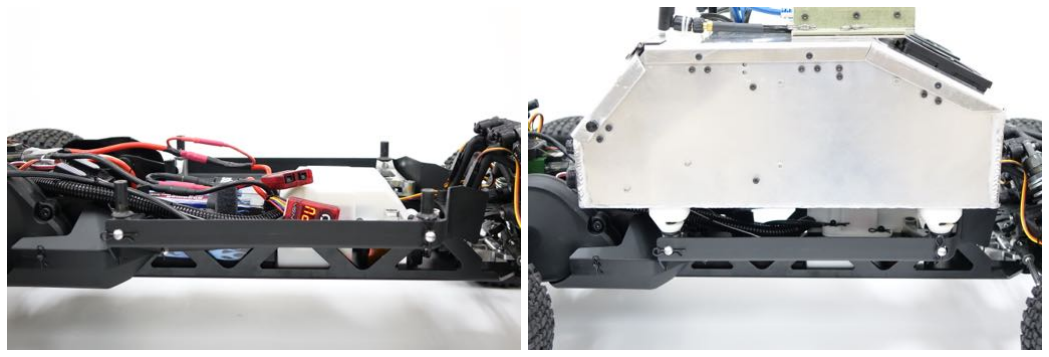
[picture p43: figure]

b. Secure compute box to chassis by pressing a large body clip through each of the four compute box chassis mounts and into the chassis body mounts.

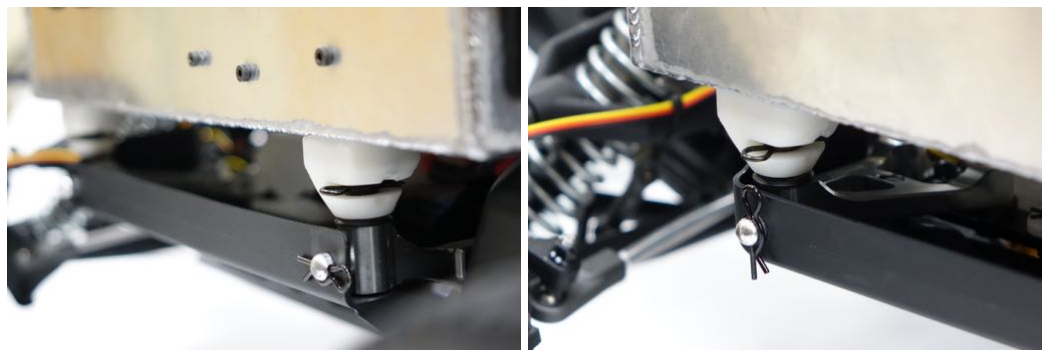
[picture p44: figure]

6 PLATFORM SETUP

### 6.4 Data Connections

Parts

- AutoRally platform
- 12-pin GPIO cable

Instructions

a. Connect one end of the 12-pin GPIO cable to the GPS box.
b. Connect the other end of the 12-pin GPIO cable to the 12-pin GPIO jack on the back of the compute box.
c. Connect the electronics box USB cable to the USB port on the back of the compute box and screw in the protective jacket.

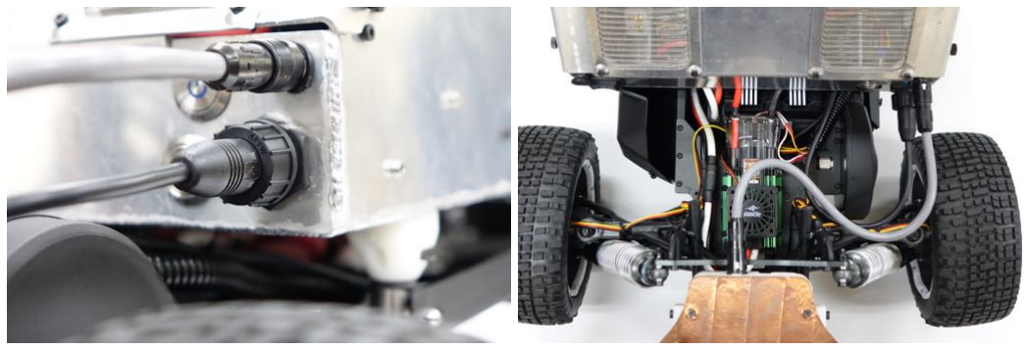
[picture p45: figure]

7 SOFTWARE CONFIGURATION

## 7 Software Configuration

The platform should already be configured with the AutoRally Platform Configuration. (https://github.com/AutoRally/autorally/wiki/Platform%20Configuration%20Instructions)

### 7.1 System Boot

Parts

- Compute box
- Monitor, keyboard and mouse setup

Instructions

a. If desired, connect the monitor and keyboard to the compute box. The display drivers may not load if a monitor is not plugged in on boot. To connect a monitor after booting, ssh into the compute box and run the command:

sudo service lightdm restart

b. Apply power to the compute box with either shore power or battery power.
c. Turn on the compute box by pressing the power button on the rear panel of the compute box.
d. Turn on the OCS computer.
e. Ping the AutoRally platform from the OCS computer to confirm network connectivity. If network connectivity fails, refer to the Configuring IP Addresses for the AutoRally Platformpage. (https://github.com/AutoRally/autorally/wiki/Platform%20Configuration%20Instructions)

7 SOFTWARE CONFIGURATION

### 7.2 Launch Core Software

Instructions

a. In a terminal window on the OCS computer, source the configuration file for the AutoRally platform you will control. If you’ve already set up an alias for the platform during the AutoRally Platform Configuration, use the alias instead. Verify that the output from the configuration script shows the expected values, i.e. that the correct chassis and cameras were detected. This step must be done in every new terminal window.
b. Launch the core software for the platform from the terminal you just configured on the OCS computer with the command:

roslaunch autorally core autorally . launch

c. Launch the cameras in another terminal window on the OCS computer with the command:

roslaunch autorally core cameras . launch

d. Verify the cameras are publishing data correctly with either the OCS or the rqt image view tool:
- In the OCS, open the video tab, click refresh, and select a topic. Or,
- launch the rqt image view tool with the command below, click refresh, and select a topic.

rqt image view

e. The topics to view are the /left camera/image raw and /right camera/image raw topics. Use the compressed versions when connected over the network, /left camera/image raw compressed and /right camera/image raw compressed respectively.
f. If the images do not show, in the System Info tab in the OCS, check the camera nodelet manager: /CameraTrigger. Verify the triggering rate requested and the actual triggering rate are their expected values. If there is an issue with the triggering, triggering can be disabled. Launch the dynamic reconfiguring tool with the command:

rosrun rqt reconfigure rqt reconfigure

g. In the tool, select left camera nodelet on the left and scroll down to the bottom. Uncheck the box labeled enable triggering. Repeat this process for right camera nodelet.
h. If desired, record data with rosbags. Refer to the ros documentation to record the desired topics. Recording raw image topics takes a large amount of memory. Consider only recording the compressed images.

### 7.3 Time Synchronization

Instructions

a. Locate the Diagnostic Messages display in the System Info tab of the OCS GUI. Verify that the GPS has signal by looking at the GPGNS GPS mode indicator value in the diagnostic entry of gpsRover:/gpsRover/primaryPort and ensuring that it displays ”R-RTK fixed integer converged”. This may take some time depending on your location and equipment. Any GPS fix type (RTK, di↵erential, or automatic) is sucient to continue with the time synchronization process.
b. This step is performed on the AutoRally compute box. You can SSH into the AutoRally compute box from the OCS computer or use the monitor, keyboard, and mouse

8 DRIVING CONTROLS

connected to the compute box. Synchronize compute box system with GPS time with the following commands in a terminal window:

Configure the USB port gpsd will use to communicate with the GPS.

stty 115200 < /dev/arGPSroverPortB

Launch gpsd

sudo gpsd /dev/arGPSroverPortB n

c. On the compute box, verify that chrony is synchronizing the compute box system time with GPS time with the following commands:

Start the chrony client.

chronyc

Chrony client command that lists the time sources that the chrony daemon synchronizes itself to.

sources

d. Repeat step c on the OCS computer to verify that OCS system time is synchronizing to the compute box system time.
e. Wait until the clocks are synchronized. Synchronization is achieved when one of the pps sources has a asterisk next to a pound symbol). On the OCS, a caret is displayed instead of an asterisk next to a pound symbol.

If the OCS computer does not appear to be synchronizing its clock with the compute box, restart the OCS computer.

### 7.4 Launch Base Station Software

Instructions

a. Launch the base station software on the OCS computer in a configured terminal with the command:

roslaunch autorally core baseStation . launch

b. Use the OCS GUI to verify that all nodes/software are functioning properly. Then disconnect the monitor, keyboard, mouse, etc. from the platform.
c. Plug all exposed compute box panel connections before placing the platform on the track. Place the platform on the track, with the car body secured on the platform with body pins.

## 8 Driving Controls

Reference the Transmitter Operation subsection under the Getting Started section for detailed information about operating the transmitter.

10 PLATFORM SHUTDOWN

### 8.1 Manual Controls

Parts

- Futaba 4PLS transmitter
- Powered AutoRally platform

Instructions

a. Enable motion with SW1 on the transmitter grip.
b. To operate the AutoRally platform with the transmitter in Manual mode:

Steering: rotate the wheel on the transmitter

Throttle: pull the trigger toward the transmitter grip

Brake: push the trigger away from the transmitter grip

### 8.2 Autonomous Control

Instructions

a. Enable motion with SW1 on the transmitter grip.
b. Set the Manual/Autonomous control switch on the transmitter to Autonomous mode.
c. Enable motion within the OCS window by pressing the large ”Enable Motion” button.
d. Enable motion on the run-stop box by releasing the red mushroom button, followed by pressing the green button. Verify that motion is enabled by checking that the RunStop Motion Enabled button of the OCS is green. Refer to Run-Stop Box Operation for run-stop box details.
e. The system is now ready to be controlled autonomously.

## 9 What’s Next

Refer to the AutoRally Wiki (https://github.com/AutoRally/autorally/wiki) for tutorials about the AutoRally state estimator, waypoint follower, and constant speed controller.

## 10 Platform Shutdown

### 10.1 Software

Parts

- Running OCS computer
- Running AutoRally platform

Instructions

a. Shut down all software running and close out any terminal windows on the compute box and OCS computer.
b. Shut down OCS computer.

11 TEST SITE CLEANUP

### 10.2 Compute Box

Parts

- Running compute box

It is very important to place connector caps on open connectors as you unplug batteries. Instructions

a. Shut down the compute box by pressing the compute box power button.
b. Set the compute box battery switch to position 0 to disable battery power.
c. If compute box is running on shore power, remove shore power cable.
d. Disconnect the 12-pin GPIO cable from the GPS box and compute box.
e. Disconnect the electronics box USB cable from the compute box.
f. Remove monitor, keyboard and mice connections from the compute box.
g. Once all external connections to the compute box are removed, remove the large body pins from the chassis mounts and unmount compute box from the chassis.
h. Remove the two thumb screws from the rear hinge panel of the compute box and open rear hinge panel to access compute box battery.
i. Unplug and cap the positive connector of the compute box battery.
j. Unplug and cap the ground connector of the compute box battery.
k. Remove the compute box battery from the compute box and place it in a LiPo sack.

### 10.3 Chassis

Parts

- Running AutoRally chassis
- Battery plugs

Instructions

a. Unplug and cap the 4mm pre-charge connector.
b. Unplug and cap the 6.5mm positive (red) connector.
c. Unplug and cap the 6.5mm ground (black) connector.
d. Disconnect LiPo monitors.
e. Remove batteries from the chassis.
f. Remove the Baja series adapter.
g. Place batteries in protective LiPo bags.
h. Power o↵ the transmitter.

## 11 Test Site Cleanup

Instructions

a. Disassemble Base Station GPS.

12 IN LAB POST-RUN

b. Disassemble Wireless Access Point setup.
c. Disassemble OCS computer.
d. Remove any monitors, keyboards, mice, wires, tables, etc. from the test site and pack up any other tools and equipment used.

## 12 In Lab Post-Run

### 12.1 Hardware Post-Run

Parts

- AutoRally chassis
- Compute box

Instructions

a. Clean dirt and debris o↵ of platform. If there is dirt inside the compute box, blow it out with a compressed air can.
b. Clean compute box fan filters (located on the compute box lid). Refer to the Cleaning Fan Filter subsection at the end of this section for detailed instructions.
c. Remove and clean plastic under guard and engine guard from the chassis.
d. Inspect platform for loose screws, damaged parts, or any other mechanical or electrical issues. Pay special attention to:

Cracks in chassis 3-D printed mounts

Screws at the bottom of the chassis

Damaged electrical connectors

Rubber components in axle boots and shock boots

e. After removing batteries, make sure that they are stored in an appropriate place.

### 12.1.1 Clean Fan Filters

Parts

- Compute box
- Fan filter cover with fan filters
- Compressed air can (optional)

Instructions

a. Locate the fan filters on top of the compute box.
b. Release bottom, left, and right tabs of the filters cover by pulling up on them.

12 IN LAB POST-RUN

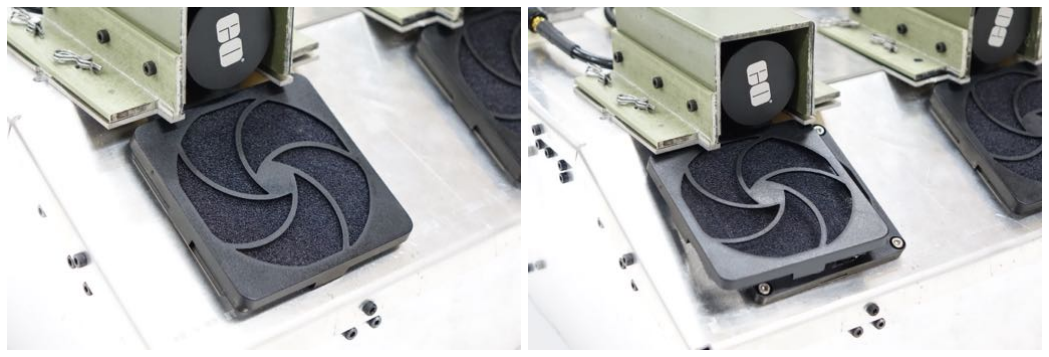
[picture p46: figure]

c. Slide filter covers sideways underneath camera covers to remove.
d. Remove and wash the filter in water, or by blowing out the dust with compressed air.
e. Reinstall filter and cover by reversing the above instructions.

### 12.2 Software Post-Run

Parts

- Compute box with monitor, keyboard, and mouse setup
- OCS computer

Instructions

a. Power up the AutoRally platform in lab.
b. Move all recorded data from the compute box.

12 IN LAB POST-RUN

c. Commit any changes made to software.

13 APPENDIX A: TEST-RUN CHECKLIST

## 13 Appendix A: Test-run Checklist

### 13.0.1 Pre-run

- Charge the chassis and compute box batteries.
- Update software on the compute box and the OCS laptop.
- Perform a full distributed launch to ensure all the necessary hardware and software is working correctly.
- Pack all the necessary equipment.

### 13.0.2 Test-run

- Set up the ground station on site (chairs, tables, large tent, etc.).
- Set up the wireless access point.
- Set up the GPS base station.
- Install the chassis and compute box batteries.
- Mount the compute box.
- Attach the USB and the 12-pin GPIO cables to the compute box.
- Start the computer and launch the core software.
- Synchronize the computer clocks.
- Launch the base station software.
- Start the desired ancillary software.

### 13.0.3 Post-run

- Shut down the compute box.
- Remove the chassis and compute box batteries.
- Disassemble the ground station.
- Clean the hardware including air filters.
- Upload testing data.

14 APPENDIX B: PARTS

## 14 Appendix B: Parts

- 24V MaxAmps power supply
- 6.5mm battery cable adapters
- AutoRally chassis
- AutoRally mini-ITX compute box

14 APPENDIX B: PARTS

- Baja series adapter
- Car body
- Cable plugs
- Chassis batteries - LiPo 6500mAh 4S 14.8v HPI Baja Pair

14 APPENDIX B: PARTS

- Compute Box battery - LiPo 11,000mAh 6S 22.2v battery
- Electronics box
- Electronics box USB cable, waterproof Type A Male

14 APPENDIX B: PARTS

- Futaba 4PLS transmitter
- GPIO 12-pin cable
- GPS box
- GPS RS320 receiver

14 APPENDIX B: PARTS

- GPS Antenna (L1/L2 GPS, L-Band)
- GPS TNC-TNC antenna cable
- GPS DB-9 data cable with serial to USB adapter

14 APPENDIX B: PARTS

- GPS USB cable, Type-A to Type-A
- GPS power adapter
- Hyperion EOS 720i battery charger
- Large body clips

14 APPENDIX B: PARTS

- LiPo monitor
- Power over Ethernet (PoE) injector
- PoE injector power supply

14 APPENDIX B: PARTS

- Run-Stop box
- Shore power cable
- Wireless Access Point (AP)

16 APPENDIX D: CONTRIBUTORS

## 15 Appendix C: Revision History

Revision | Date | Author(s) | Description
1.1 | July 2016 | LP, AL, BG | created, version aligned with other documenta-
| | | tion
1.2 | September 2016 | BG | Spelling fixes
1.3 | February 2017 | DP, JZ, BG | Streamlined procedure and added hints

## 16 Appendix D: Contributors

Brian Goldfain
Alexandra Lin
Dominic Pattison
Luis Pimentel
Justin Zheng

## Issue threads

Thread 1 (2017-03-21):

Incomplete instructions regarding front-brake installation

ljb2208, 2017-03-21:
The chassis instructions document does not have complete documentation of the optional front-brake installation. In particular where the brake servo should be placed.

bgoldfai, 2017-03-21:
Thanks for catching this! If you're building the platform we'd love to get any major or minor feedback and pictures of your build. For now, use the instructions below and the attached images. This step will be part of the document for the next update. Let me know how this works.

Parts:
- 3 M3x10mm screws
- 4 M4x14mm screws (same as for the motherboard in the compute box)
- 4 M4 nuts
- 2 M4x6mm screws (can use M4x14 from above and just pad with washers if needed)
- 2 (or more) M4 washers
- Throttle pivot set
- Brake rod set
- F 25 servo horn that came with the Baja (25 tooth for Futaba)
- Bleed valve cap
- Servo Cable
- 1 Futaba J connector assembly (2 3x1 housings, 1 connector cover, 3 male 0.1" crimps, 3 female 0.1" crimps)

Instructions:
- Remove the 3 M3 button head screws from the left, top of the conversion kit top plate
- Use the 3 M3x10mm screws to secure the servo and master cylinder mounts to the chassis using the stock holes in the conversion kit top plate
- Install the servo with 4 M4x14mm screws and 4 M4 nuts
- Install the master cylinder with the 4 M4 washers and 2 M4x6mm screws. If using longer M4 screws, just pad with additional washers.
- Install brake rod and pivot linage as shown in picture with servo horn parallel to master cylinder arm
    - You may have to use a longer M3 screw than came in the pivot set to attach the pivot to the servo horn.
    - When installing the servo horn, try to make the servo neutral position put no or very light pressure on the brake servo linkage. This can be adjusted again later once the servo is powered)
- Make 10" servo extension cable with Futaba J connector assembly, connect to brake servo cable, and route through split loom into the electronics box with other cables coming from the back of the chassis.
- Cut the brake rod so that it doesn't extend beyond the linkage
- You will likely have to cut a little of the motor shroud to allow the linkage to freely actuate once the shroud is reinstalled.
- Follow normal instructions for connecting brake lines and bleeding
- Secure brake line with a few zip ties to the chassis
- Install bleed valve cap once done bleeding

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

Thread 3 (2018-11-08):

GPS Model Discontinued

clarkr28, 2018-11-08:
It appears that the GPS on the V1.4 parts list, the Hemisphere Eclipse P307, has been discontinued and replaced with a new model called the Eclipse P327 - see link [here](https://www.navtechgps.com/eclipse_p306_and_p307_oem_module/).  Would someone be able to confirm that the new model is compatible?

clarkr28, 2018-11-08:
Also, could you explain why we need to order the 'Hemisphere GNSS OEM Board Universal Development Kit with activations'?

bgoldfai, 2018-11-09:
It looks like the P327 should be able to replace the P307, but we don't have a P327 to test ourselves. The two boards have the same form factor so mounting and power should be the same, but the 20 pin connector on the P327 appears to have a different pin spacing which may require a different ribbon cable. I don't see the technical documentation for the P327 which should have the connector part number to look up and compare to the ribbon cable on the AutoRally parts list.

Hemisphere usually offers a discount on the first couple P307 UDK kits an organization purchases that makes it significantly cheaper than purchasing just a P307 board. You don't actually need any of the other parts that come in the UDK. I don't know if that same package is available for the P327.

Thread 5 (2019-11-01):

The HPI Baja 5SC chassis is discontinued.  Would you recommend a replacement

zhenzjia, 2019-11-01:
Would you recommend a suitable replacement for the Baja 5SC chassis. Thanks!

nolanwagener, 2019-11-01:
The [HPI Baja 5SC product page](http://www.hpiracing.com/en/kit/105235) says that it has been replaced by the RTR Baja 5SC. I can't find any information on the form factor of the RTR, so I can't say whether it would be a suitable replacement.

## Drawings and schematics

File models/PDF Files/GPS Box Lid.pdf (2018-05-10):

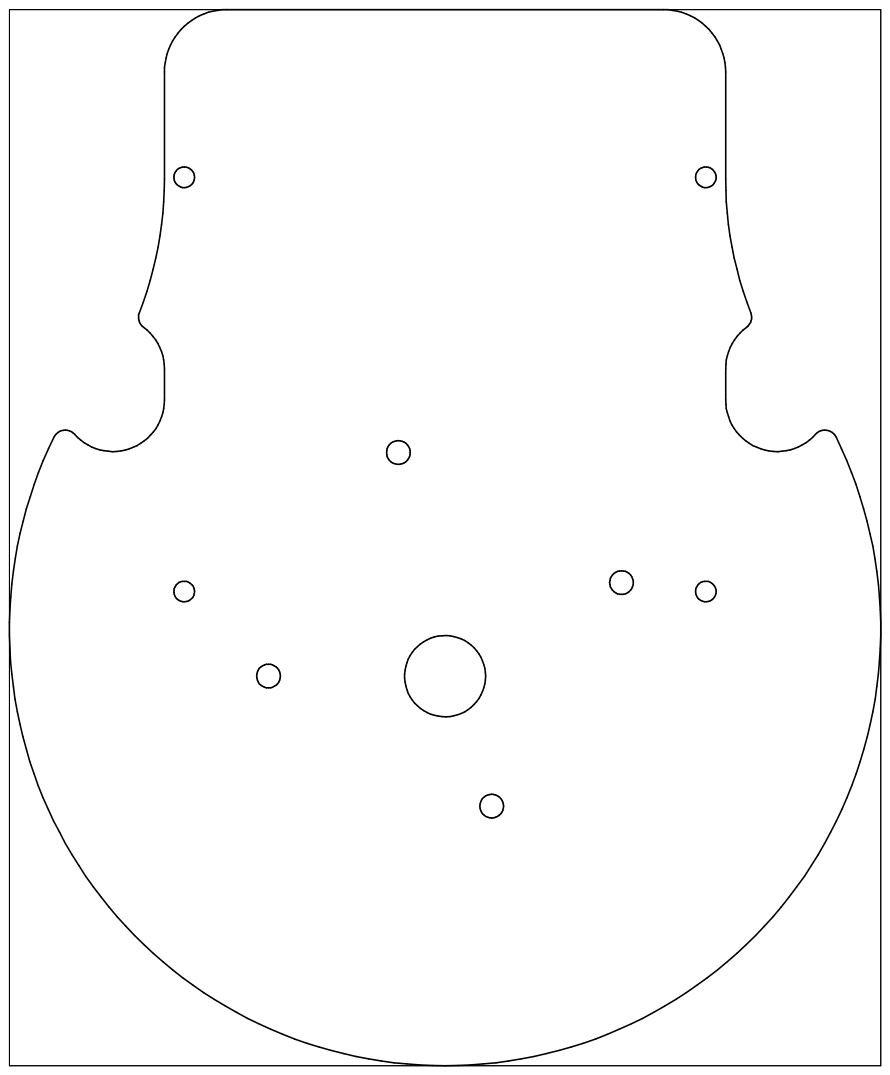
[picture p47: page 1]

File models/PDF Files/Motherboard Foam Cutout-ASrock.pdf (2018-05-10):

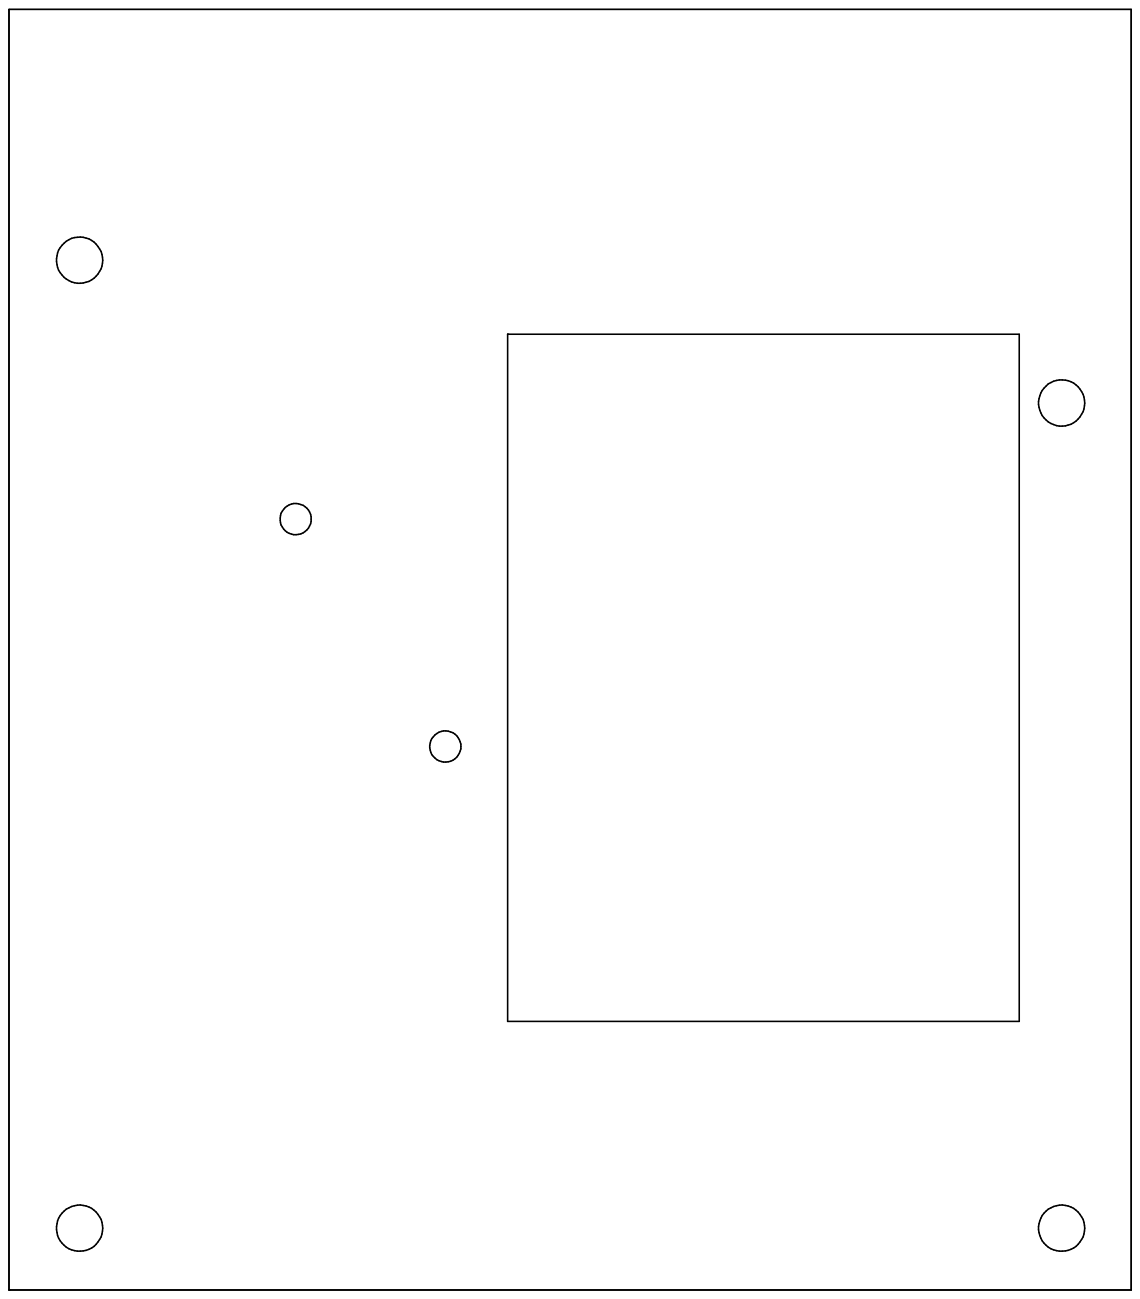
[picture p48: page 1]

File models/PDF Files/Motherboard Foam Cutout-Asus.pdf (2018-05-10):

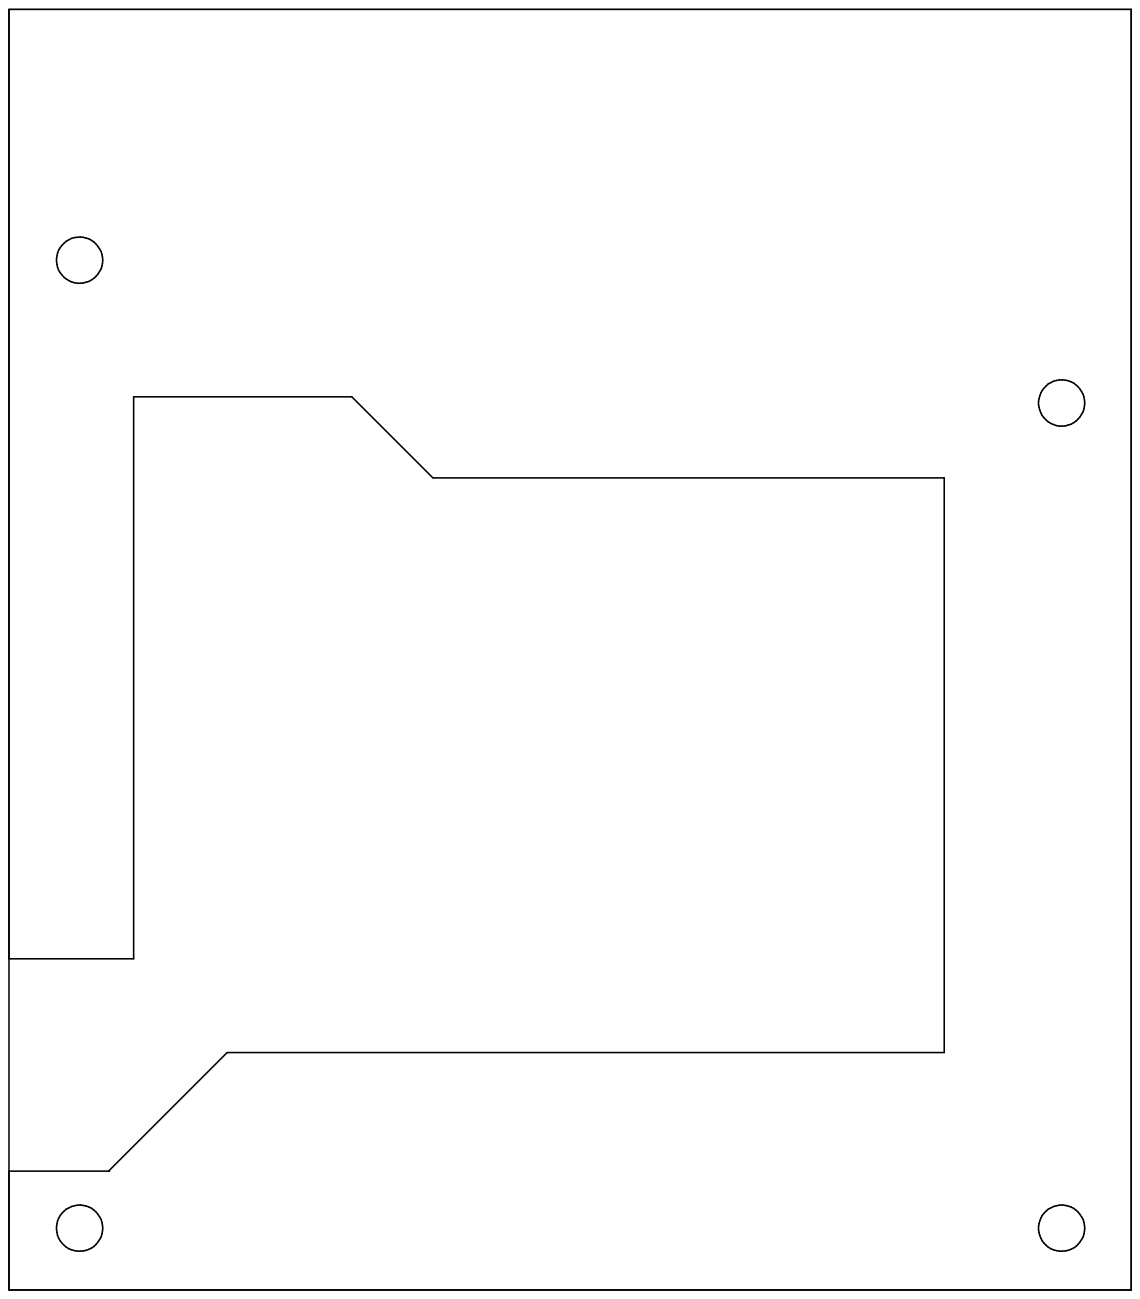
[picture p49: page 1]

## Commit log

2016-05-25 Initial commit for instruction documents
    [AutoRallyPartsList.xlsx, Bullet Connector Cover.stl, Bullet Connector Mount.stl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]
2016-07-28 Updated everything for 1.1 release
    [Arduino Micro Cover Top Plate.stl, Arduino Micro Cover.stl, AutoRallyPartsList.xlsx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]
2016-09-20 v1.2
    - Fixed error in compute box wiring diagram
    - cleaned up spelling mistakes
2017-03-14 AutoRally platform documentation v1.3
    [Front Brake Servo Mount.stl, Master Cylindar Plate.dxf, autoRally_platform_parts_list.xlsx]
2018-03-05 Updated wiring diagrams
2018-03-05 Preliminary updateded parts list for version 1.4
    [AutoRallyPartsList.xlsx]
2018-03-05 removed v1.3 parts list and renamed new parts list
    [AutoRallyPartsList.xlsx, autoRally_platform_parts_list.xlsx]
2018-05-10 Updated Parts list
    [autoRally_platform_parts_list.xlsx]
2018-05-10 new stl files for 3D printing V1.4
    [Arduino Micro Cover Top Plate.stl, Arduino Micro Cover.stl, Brake Disk Aligner - Left.stl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]
2018-05-10 Updated files for aluminum parts cut on waterjet, separated out individual parts instead of having large cut patterns
    [Camera Mount Bracket.dxf, Compute Box Aluminum 3003 090 Cut Pattern.dxf, Compute Box Aluminum 6061 025 Cut Pattern.dxf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]
2018-05-10 Added V1.4 files for laser cut components, now as pdf files instead of dxf
2018-07-19 minor updates to parts list, only ecpected update for V1.4 release will be different USB isolator
    [autoRally_platform_parts_list.xlsx, autorally_platform_parts_list.xlsx]
2018-09-17 Updating instructions documents and supporting files for V1.4. Only remaining document not yet updated is Operating Procedures
    [autorally_platform_parts_list.xlsx]
2019-01-24 Added missing dxf files for gpu strut and compute box brace
    [Compute Box Brace.dxf, GPU Strut.dxf]
